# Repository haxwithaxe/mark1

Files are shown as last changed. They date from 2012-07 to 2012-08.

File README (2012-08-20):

INSTRUCTIONS

First, safety warning: this thing uses rare earth magnets, so be extremely careful when putting it together — you can easily lose a finger or worse if one magnet attracts another.

You'll need:

 * 16 1/4" x 4" ID x 8" OD rare earth wedge magnets; you can get these from magnet4less.com or aliexpress.com if you're outside the US.
 * About 5lbs (2kg) of 12AWG (19SWG) copper magnet wire; you can get this from bulkwire.com.
 * 1 tube of gasket sealant from any hardware store
 * Wire cutters (scissors will do in a pinch)
 * Electrical tape
 * Optionally: kapton tape and a soldering iron
 * 2 rotor plates in 5mm stainless steel; the cheapest way to get these is to order them from someone with a CNC mill, which is completely dependent on where you're located. The cheapest online 3D printer for stainless steel is ponoko, but it's still very expensive (>$500)
 * 16 rotor.stl pieces, printed
 * 16 rotor_edge_tie.stl pieces, printed
 * 4 rotor_peg.stl pieces, printed
 * 6 stator.stl pieces, printed
 * 6 chuck.stl pieces, printed
 * 2 support.stl pieces, printed (these are used in winding the induction coils and are not present in the finished product)
 * 1 rotor_cap.stl piece, printed — I highly recommend you customize this to your application

Rotor assembly:

 * Put one rotor plate on the floor.
 * Put one magnet in a rotor piece and slide it under the plate.
 * Secure the assembly with a rotor edge tie.
 * Repeat steps 2 and 3 until you have all 8 spaces filled. Make certain that you place the magnets such that each magnet attracts the ones beside it.
 * Use gasket sealant around the circumference of the rotor, where the plastic meets the metal (inside circumference and outside circumference) and leave the rotor at least 2-3 hours for the sealant to cure.
 * Repeat steps 1-4 for the other rotor plate. KEEP THE TWO ROTOR PLATES FAR APART for now; they will be extremely strongly magnetically attracted to each other.

Stator assembly:

 * Place a chuck between the two winder supports.
 8 Thread the end of your magnet wire spool through the end of the chuck. Leave plenty of extra wire (like 20cm) on the end because you'll need to connect it to a coil on the opposite side of the stator later.
 * Wind an induction coil by rotating the supports. Stop when the edge of the coil meets the edge of the support.
 * Clip the wire leading to your spool. Again, make sure to leave plenty of extra wire for later.
 * Immediately after removing the supports, keep pressure on the coil with your hand and wrap it with two pieces of electrical tape so it will retain its shape.
 * Repeat steps 1-4 six times to form 6 induction coils.
 * Place each induction coil in a stator piece and put the stator pieces together (it will be obvious how they fit if you put each one face-up on the floor oriented like they were when you printed them).
 * To wire the generator in star configuration, you will need 3 of the induction coils to have their starting wire (the part threaded through the chuck) pointing out through the stator notch. Call these the A coils. The other 3 coils need their ending wire (the part you clipped from the spool) pointing out. Call these the B coils. Set them up like this now — you may want to label which is which because you'll need to remember for the next step.
 * Connect the outer ends of the A coils together to form the star point. I recommend you use a soldering iron for this, but you can also use a wire tie if you prefer.
 * Within the stator, connect the inner ends of the A coils to the inner ends of the B coils. You may need to trim some excess; go ahead and do so now. Your goal is to keep the inner connections as low-profile as possible so they don't interfere with the rotation of the generator.
 * Glue the stator pieces together with gasket sealant. You should secure the induction coils in place somehow — I recomment kapton tape, although gasket sealant will probably work as well.
 * Leave the stator at least 2-3 hours for the sealant to cure.

Generator assembly:

 * Turn over one rotor such that the plastic side is facing up.
 * Place the stator on the rotor so that the center spaces on each line up.
 * Fit one thrust bearing into the center space. Make sure that it meshes with the rotor rather than sitting on top of it.
 * Place the second thrust bearing on top of the first. When lowering the second rotor half onto the bearing, take care to keep it aligned so that magnetic attraction doesn't dislodge the top of the bearing.
 * Lower the other rotor onto the stator, plastic-side down.
 * Fit the rotor cap to the top of the rotor, making sure the rotor peg holes line up with the holes in the rotor pieces, and glue around the perimeter with gasket sealant. Allow 2-3 hours to cure.
 * Flip the generator over, rotor cap down, and place 4 (or optionally up to 8) rotor pegs through the top rotor pieces, the opposite rotor pieces, and into the bottom of the rotor cap.

You now have a functioning 3-phase electrical generator!

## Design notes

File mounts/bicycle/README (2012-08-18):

This is designed for a specific bicycle, so you'll probably need to tweak some settings to get it to fit yours. Make sure the gear on the rotor cap matches the gear on your bicycle's back wheel.

You'll need:

 * 1 bicycle with the rear wheel removed (make sure to keep the axle handy). If the kickstand doesn't look sturdy enough to support a person without a rear wheel, get a sturdier replacement from a bike shop.
 * 1 electrical generator, thing:28762
 * 1 tube of gasket sealant

 * Print 1 mount, 1 mount_support_a, 1 mount_support_b, 1 rotor_cap, and 3 pins
 * Glue the rotor cap to the generator with gasket sealant and allow 2-3 hours to cure
 * Put together the mount and supports such that they fit snugly with the bicycle frame and the top hole is 12cm above the rear axle of the bicycle.
 * With the bicycle on its side, secure the generator to the mount with the pins and re-insert the bicycle axle. Secure with nuts/bolts as appropriate to your bicycle.

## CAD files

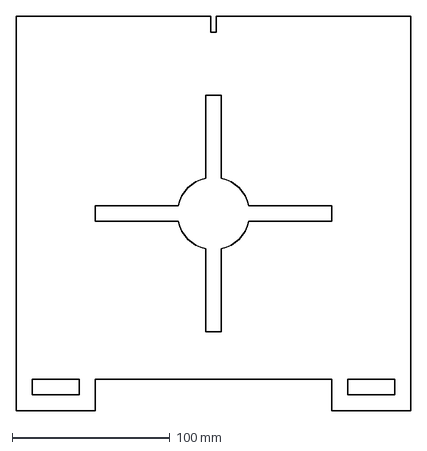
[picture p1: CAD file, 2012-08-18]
mounts/wind/mount_base.dxf
250.0 x 250.0 mm

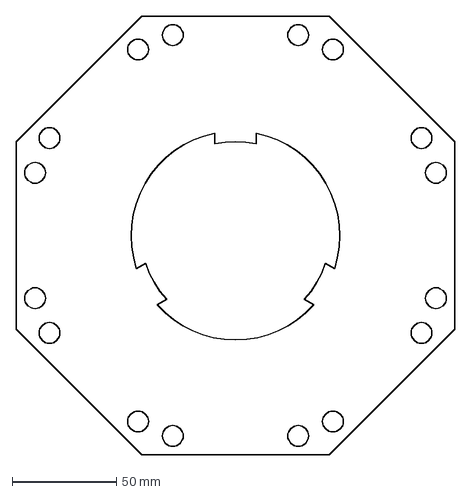
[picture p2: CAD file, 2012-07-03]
rotor_plate.dxf
210.0 x 210.0 mm

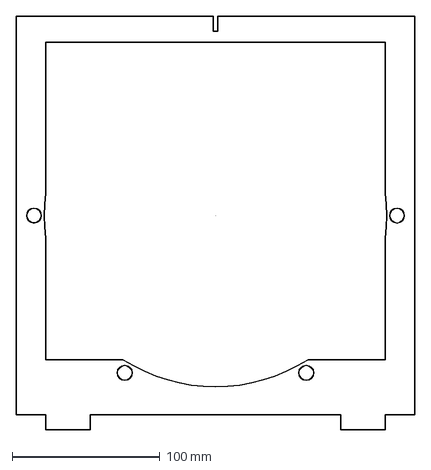
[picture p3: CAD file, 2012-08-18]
mounts/wind/mount_vertical.dxf
270.0 x 280.0 mm

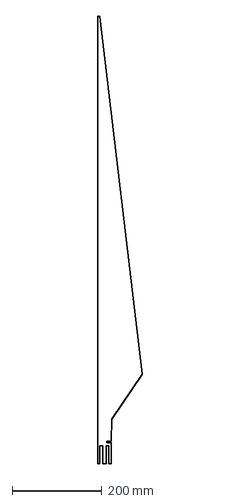
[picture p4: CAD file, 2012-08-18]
mounts/wind/blade.dxf
100.0 x 1000.0 mm

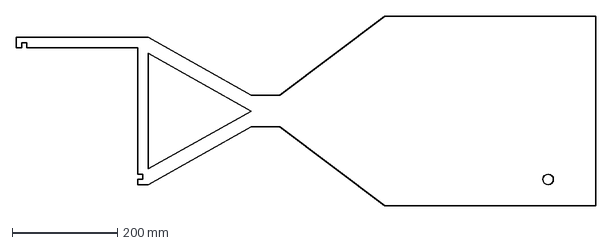
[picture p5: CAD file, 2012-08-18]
mounts/wind/vane.dxf
1100.0 x 360.0 mm

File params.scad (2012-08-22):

/*
 * Copyright (c) 2012 Haydn Vestal
 * 
 * See the file license.txt for copying permission.
 * 
 */

// GLOBAL
hole_radius = 5;
peg_radius = 4.5;

// MAGNET
mag_height = 6.4;
mag_ring_ir = 50;
mag_ring_or = 102;
mag_count = 16;

// BEARING
bearing_height = 34;
bearing_ir = 29.5;
bearing_or = 43;

// STATOR
stator_height = 16;
stator_inner_height = stator_height/2;
stator_count = 6;
stator_incidence = 360/stator_count;
stator_radius = 115;
stator_tab_width = 10;
stator_tab_offset = 50;
stator_wiring_gap = 25;
stator_wiring_gap_inset = stator_radius - (stator_wiring_gap + 10);
stator_outer_tab_extrude = 15;
stator_outer_tab_width = 30;
stator_notch = 15;
stator_notch_width = 5;
coil_edge = 80;
coil_block_length = 70;

// ROTOR & ROTOR CAP
rotor_height = mag_height + 2;
rotor_inner_height = 3;
rotor_radius = 105;
rotor_inner_radius = 20;
rotor_count = 8;
rotor_incidence = 360/rotor_count;
rotor_tie_hole_offset = 30;

rotor_cap_radius = 50;
rotor_cap_peg_radius = 35;
rotor_cap_inner_radius = 10;
rotor_cap_height = 10;
rotor_cap_insert_height = 10;
rotor_cap_bearing_inset = (bearing_height + rotor_inner_height) - rotor_cap_height;
rotor_plate_height = 5;
blade_holder_edge = 20;
rotor_peg_width = 12;
rotor_peg_height = (rotor_height * 2) + (rotor_cap_height * 2) + stator_height;

// ROTOR EDGE TIE
rotor_edge_tie_length = 40;
rotor_edge_tie_width = 20;
rotor_edge_tie_inner_height = 5;
rotor_edge_tie_height = rotor_height + rotor_edge_tie_inner_height + rotor_plate_height;
rotor_edge_tie_peg_inset = 10;

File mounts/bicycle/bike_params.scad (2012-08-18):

/*
 * Copyright (c) 2012 Haydn Vestal
 * 
 * See the file license.txt for copying permission.
 *
 */

bicycle_axis_width = 125;
bicycle_axis_radius = 10;
bicycle_strut_radius = 6.5;
bicycle_x_front_offset = 48 * (4/7);
bicycle_x_rear_offset = 48 * (3/7);
bicycle_y_front_offset = 7.6;
bicycle_y_rear_offset = 2.4;
bike_frame_height = 200;

bicycle_gear_spacing = 12.5;
bicycle_gear_teeth = 18;
bicycle_gear_thickness = 4;
bicycle_gear_circle_radius = 32;
bicycle_axis_radius = 10;

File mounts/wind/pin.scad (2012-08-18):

/*
 * Copyright (c) 2012 Haydn Vestal
 * 
 * See the file license.txt for copying permission.
 *
 */

include <wind_params.scad>
include <../../params.scad>


pin_height = frame_thickness + stator_height + (hole_radius * 2);

module pin_unadjusted() {
  difference() {
    cylinder(h=pin_height, r=peg_radius);
    translate([-peg_radius, 0, 25]) {
      rotate([0, 90, 0]) cylinder(h=peg_radius*2, r=peg_radius/2);
    }
  }
  cylinder(h=3, r=peg_radius + 3);
}

module pin() {
  difference() {
    rotate([0, 90, 0]) pin_unadjusted();
    translate([0, -peg_radius - 3, peg_radius*-2.75]) 
      cube([pin_height + 1, (peg_radius*2) + 6, peg_radius*2]);
  }
}

pin();

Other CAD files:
mounts/wind/wind_params.scad
bearing.scad
magnet.scad
mounts/bicycle/axis.scad
mounts/bicycle/bike_frame.scad
mounts/bicycle/mount.scad
mounts/bicycle/mount_support_a.scad
mounts/bicycle/mount_support_b.scad
mounts/bicycle/peg.scad
mounts/bicycle/rotor_cap.scad
mounts/wind/bearing.scad
mounts/wind/blade.scad
mounts/wind/mount_base.scad
mounts/wind/mount_vertical.scad
mounts/wind/pole_cap.scad
mounts/wind/rotor_cap.scad
mounts/wind/vane.scad
rotor.scad
rotor_cap.scad
rotor_edge_tie.scad
rotor_peg.scad
rotor_plate.scad
stator.scad
views/rotor.scad
views/stator.scad
views/turbine.scad
winder/chuck.scad
winder/support.scad

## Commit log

2012-04-05 rotor & rotor edge tie
    [magnet.scad, params.scad, rotor.scad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]
2012-04-05 added rotor cap
    [params.scad, rotor_cap.scad]
2012-04-05 added stator
    [params.scad, rotor.scad]
2012-06-10 added supplementary parts & views, changed to a needle roller bearing, and included stator in commit
    [bearing.scad, params.scad, rotor.scad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]
2012-06-29 added winder
    [base.scad, chuck.scad, handle.scad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]
2012-07-03 added DXF of rotor plate & minor improvements to winder
    [base.scad, handle.scad, rotor_cap.scad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]
2012-07-14 minor changes after using the winder
    [params.scad, rotor_edge_tie.scad, stator.scad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]
2012-07-14 MIT license
    [bearing.scad, chuck.scad, magnet.scad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]
2012-07-27 added bicycle mount, wind turbine blade, & changes to turbine to accomodate bicycle chain drive
    [axis.scad, bike_frame.scad, bike_params.scad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]
2012-08-18 added wind mount & few other minor alterations
    [bearing.scad, mount_base.dxf, mount_base.scad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]
2012-08-18 updated license
    [axis.scad, bearing.scad, bike_frame.scad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]
2012-08-18 added instructions & minor fixes
    [mount_base.dxf, mount_vertical.dxf, rotor_cap.scad]
2012-08-20 flipped rotor 180 around Y for easier printing
    [params.scad, rotor.scad]
2012-08-22 set to 60x85x17 thrust bearing
    [params.scad]
